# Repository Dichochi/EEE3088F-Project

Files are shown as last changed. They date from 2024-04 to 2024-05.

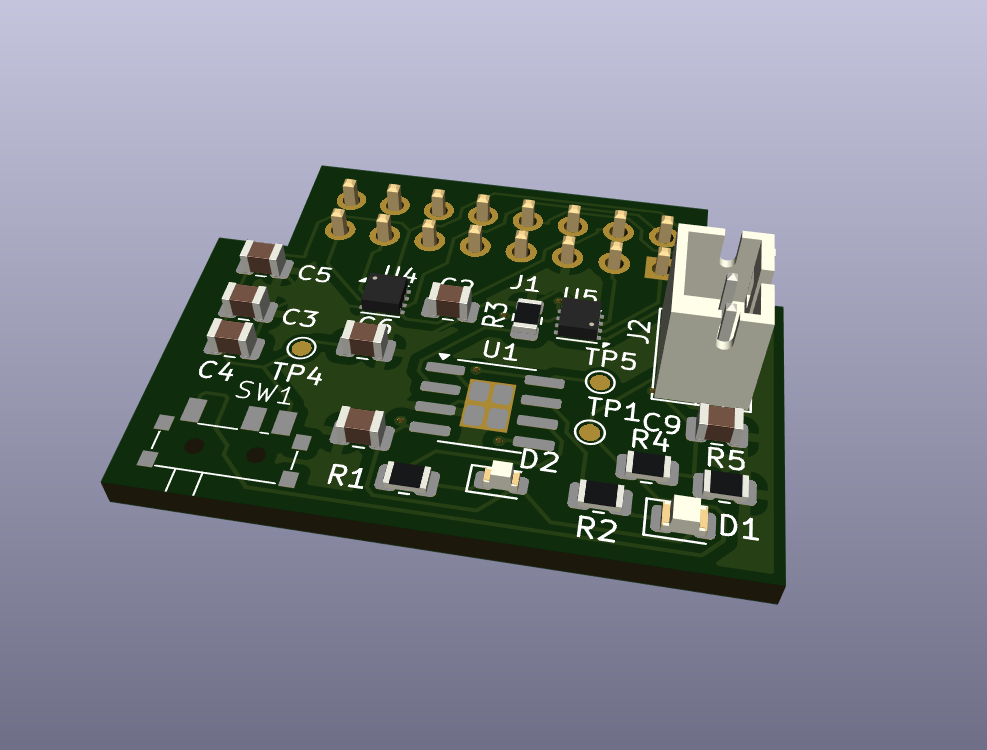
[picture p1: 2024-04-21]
Documents/Documents-Power/3D PCB.png

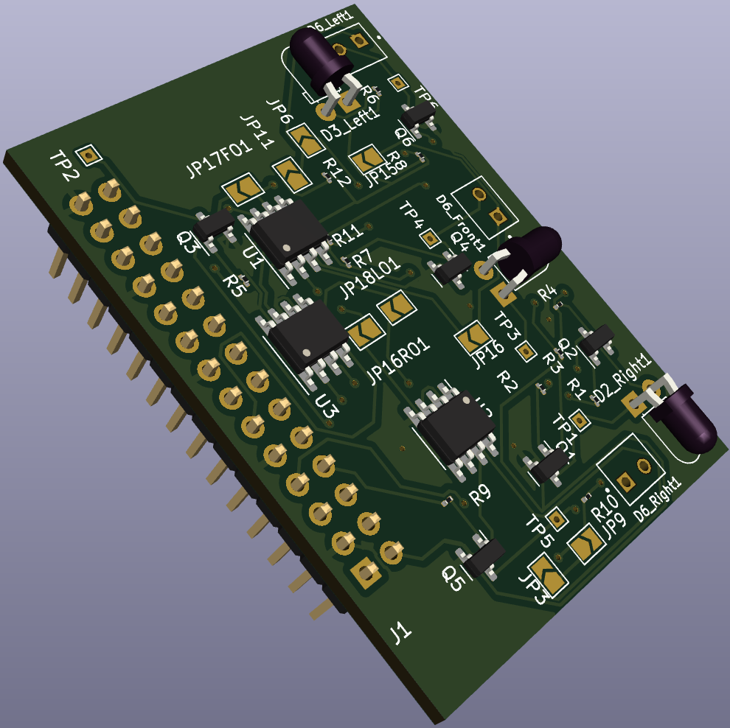
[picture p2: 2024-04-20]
Documents/Documents-Sensing/Sensor 3D view.png

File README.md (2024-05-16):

# EEE3088F-Project RMTDIC001 & NGMPHI006

## Description
This project is for the development and design of a Micro-Muse for EEE3088F 2024. The Micro Mouse contains a sesning Module, Power Module, as well as the main control unit(Mother-Board). The sensing system will sense obstacles in the proximity of the mouse, while the power module is mainly for powering the motors of the mouse and charging the on-board battery of the mouse. 

## Structure
* PCB: The KiCAD Project, Schematics & Layout and Project Libraries
* Firmware: Any software developed for the hardware or instructions on where to find relevant sofware
* Documents: Project documentation and component datasheets
* Production: The gerber files, BOM, Budget, or anything required by the fabrication houses
* Simulation: Any simulation files (eg SPICE) or design stage generated results (Eg matlab or excel) 

## Installation
--To be updated-- 

## Usage
The project documentation can be found in the [Documents](https://github.com/Dichochi/EEE3088F-Project/tree/main/Documents) directory and the files required to produce the PCB can be found in the [Production](https://github.com/Dichochi/EEE3088F-Project/tree/main/Production) directory.

## Contact
* Dichochi Ramotlou- RMTDIC001@myuct.ac.za
* Philasande Ngema - NGMPHI006@myuct.ac.za

## Project Status and Roadmap
This project is actively under developement.

## Authors and Acknowledgement
Authors:
* Dichochi Ramotlou
* Philasande Ngema

## License
[Creative Commons Attribution 4.0 International license](https://choosealicense.com/licenses/cc-by-4.0/)

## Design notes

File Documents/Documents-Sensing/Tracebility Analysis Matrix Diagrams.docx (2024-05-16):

R003:
The Sensor board should be the correct size for the Mouse.

AT002:
The freedom of movement of the Mouse should not be restricted by the sensor board., I.e. the Mouse is able to move around the maze.

SP003:
Using a board with dimensions not exceeding 40x70mm.

Verified by

Fulfilled by

AT003:
A significant change in the output when the obstacle is within an 80mm range, indicating that the ADC has captured the sense output.

R005:
The Mouse should be able to detect dead ends in the Maze.

SP002:
Three sets of sensing components a sensing range of 0-150mm, and angle spectrum of 0-60 °

Verified by

Fulfilled by

Why?

A maze dead end would be an obstacle in all three sense directions, if all the three sensing components are properly and equally calibrated, they should sense obstacles in their respective directions.

AT004:
Testing the switching behavior of the output.

SP001:
Utilizing PWM or input switching behavior so sensor turns on/off at a specific frequency and duty cycle of 50%.

R001:
Minimize Power Consumption.

Verified by

Fulfilled by

How?

The input square wave will have a duty cycle of 50%, for example if the Mouse remains on for 60s, the sensor will be off for 30s saving a lot of power.

AT001:
Observable change in output when obstacle is within 150mm of the mouse.

R004:
The Sensor board should be the able to communicate with the control unit using the correct communication protocol.

SP004:
Using I2C protocol on all ICs on the sensor board.

Verified by

Fulfilled by

Why?

To show that the sensor board works correctly an output should be observed if there is an obstacle in any of the sense directions.

AT001:
Observable change in output when obstacle is within 150mm of the mouse.

SP002:
Three sets of sensing components a sensing range of 0-150mm, and angle spectrum of 0-60 ° .

ROO2:
Valuable Sense Output from left right and forward directions.

Verified by

Fulfilled by

AT005:
The sensor should detect objects at oblique angles.

Fulfilled by

Verified by?

Although the sensing range is 150mm, what is eventually needed is a 0 or 1 to either light up an LED or turn it off when there is no obstacle, a close obstacle would be within 50mm of the Mouse.

Why?

Verified by

SP005:

Observable output voltage on ADC for all three sense directions.

AT003:
A significant change in the output when the obstacle is within an 80mm range, indicating that the ADC has captured the sense output.

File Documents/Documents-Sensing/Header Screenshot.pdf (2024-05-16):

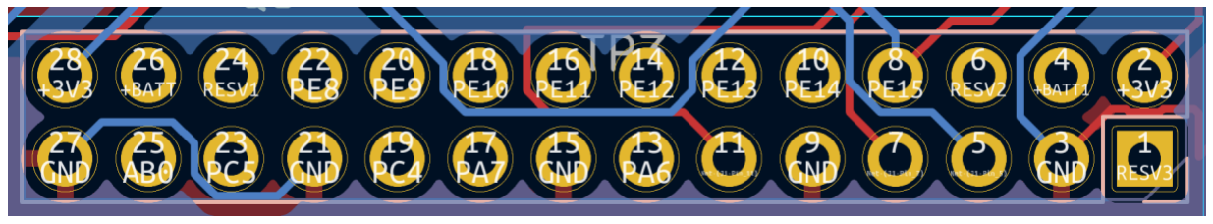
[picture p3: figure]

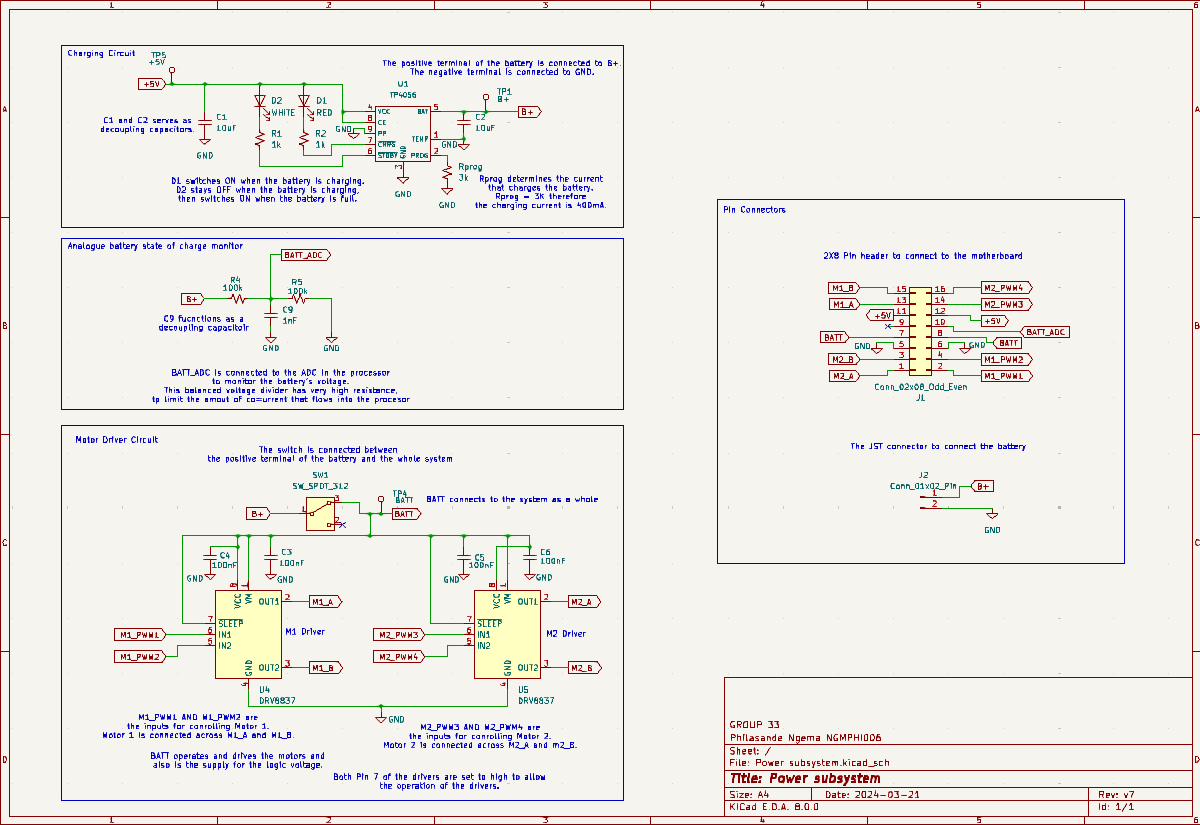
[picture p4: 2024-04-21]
Documents/Documents-Power/Final Schematic (1).png

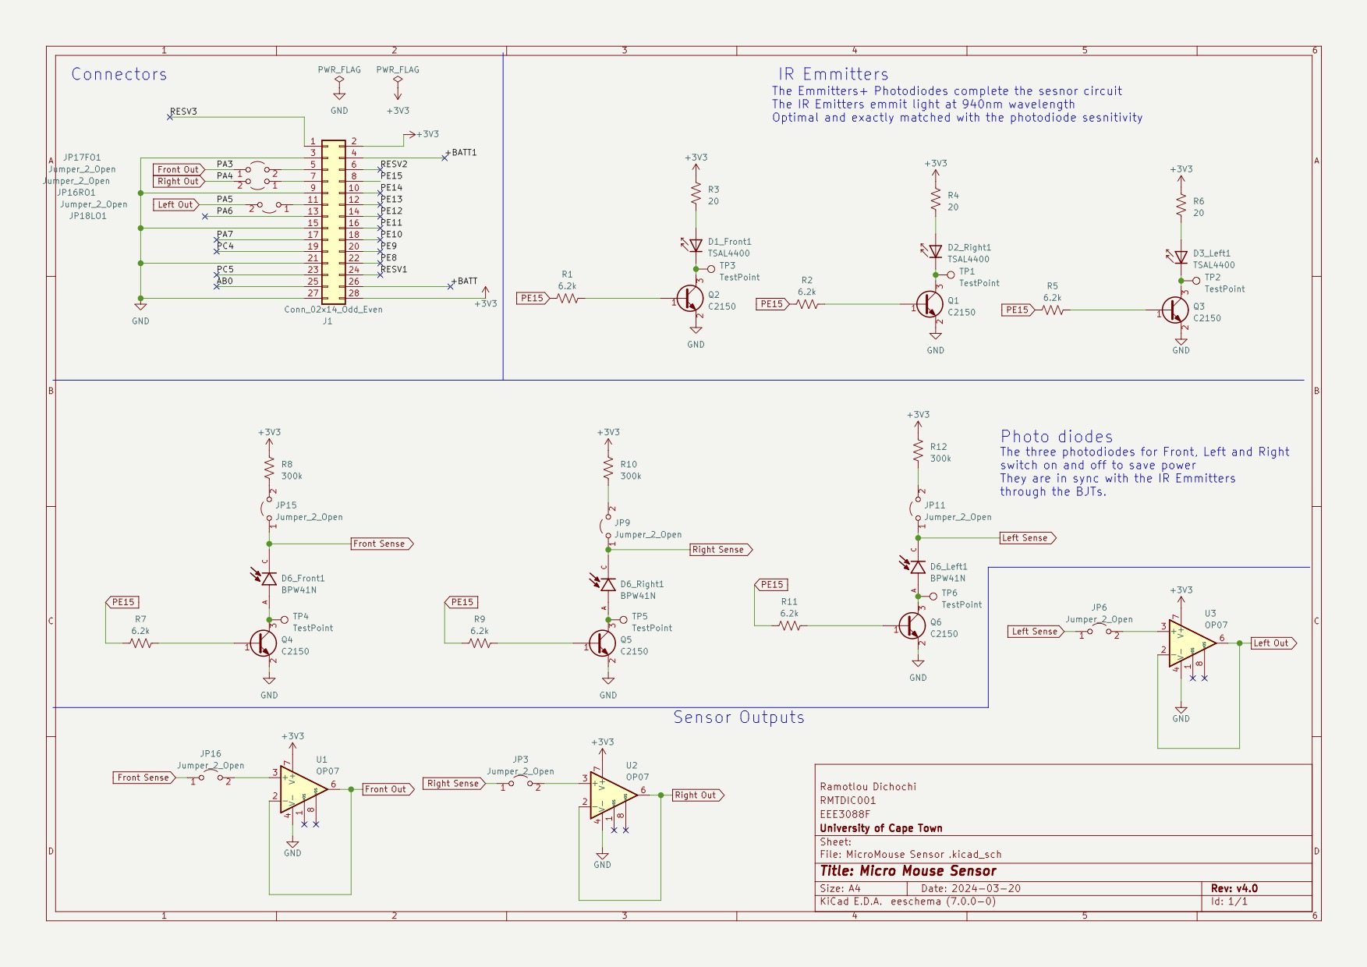
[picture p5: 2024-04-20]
Documents/Documents-Sensing/Sensor Mouse Schematic.jpg

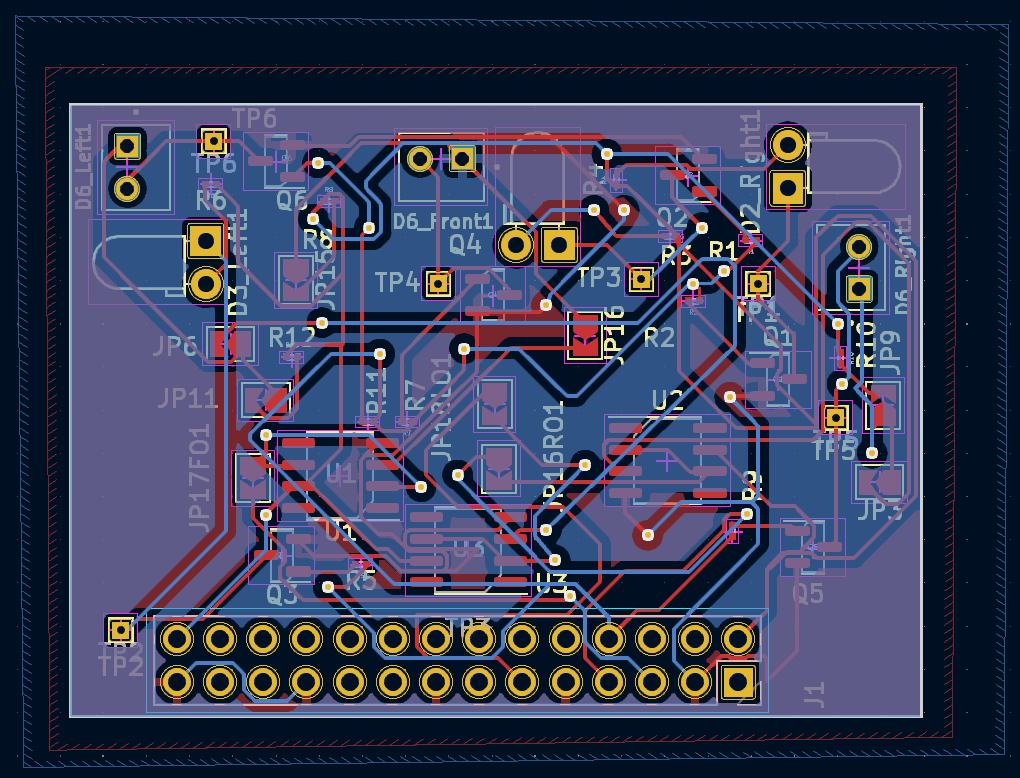
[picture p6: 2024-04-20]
Documents/Documents-Sensing/Sensor Back View .png

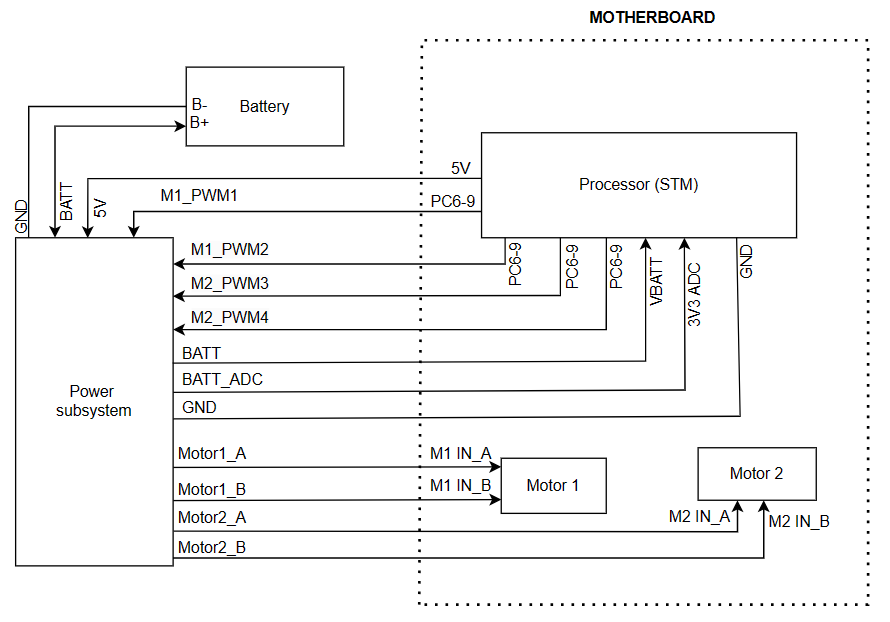
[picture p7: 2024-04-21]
Documents/Documents-Power/System Interfacing Diagram2.png

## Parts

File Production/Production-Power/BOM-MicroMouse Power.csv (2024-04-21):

Comment | Designator | Footprint | LCSC
100nF | C5 | C_0805_2012Metric
100nF | C4 | C_0805_2012Metric
100k | R4 | R_0805_2012Metric
DRV8837 | U5 | WSON-8-1EP_2x2mm_P0.5mm_EP0.9x1.6mm
RED | D1 | LED_0805_2012Metric
3k | R3 | R_0805_2012Metric
10uF | C2 | C_0805_2012Metric
100nF | C3 | C_0805_2012Metric
1nF | C9 | C_0805_2012Metric
1k | R1 | R_0805_2012Metric
DRV8837 | U4 | WSON-8-1EP_2x2mm_P0.5mm_EP0.9x1.6mm
1k | R2 | R_0805_2012Metric
10uF | C1 | C_0805_2012Metric
100k | R5 | R_0805_2012Metric
SW_SPDT_312 | SW1 | mySwitch
100nF | C6 | C_0805_2012Metric
TP4056 | U1 | SOIC-8-1EP_3.9x4.9mm_P1.27mm_EP2.29x3mm
WHITE | D2 | LED_0603_1608Metric

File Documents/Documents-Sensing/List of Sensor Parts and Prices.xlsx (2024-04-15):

Part | Mnaufacturer Code | JCLPCB Code | Quanity | Price | Extended Fee | Total
Op amp | OP07CDR | C7433 | 3 | 0.1593 | 0 | 0.4779
BJT | SS8050 | C2150 | 6 | 0.0139 | 0 | 0.0834
Photodiodes | BPW41N | C142586 | 3 | 0.489 | 1.5 | 2.967
IR Emmitter | TSAL4400 | C94135 | 3 | 0.1262 | 1.5 | 1.8786
6.2k Resistor | 0603WAF6201T5E | C4260 | 6 | 0.0009 | 0 | 0.0054
20 Resistor | 0603WAF200JT5E | C22950 | 3 | 0.0009 | 0 | 0.0027
300k Resistor | 0603WAF3003T5E | C23024 | 3 | 0.001 | 0 | 0.003
Total: | 5.418

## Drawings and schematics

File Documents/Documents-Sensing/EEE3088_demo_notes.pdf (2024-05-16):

## EEE3088F RMTDIC001 Demo Notes

FOR THE STM32

PA0-> LEFT ->LED7
PA1-> MIDDLE ->LED6
PA2-> RIGHT ->LED5

DON’T FORGET TO COMMON GROUND STM, SENSOR AND POWER SUPPLY

System Interface Input

Table 1: System Interface Table Sensor Board Input

Origin | Destination | Use
3V3 Supply | Pin 2(Sensor Board) | Power
GND Supply | Pin 3(Sensor Board) | Power
GND Supply | STM Ground Pin | Power
3V3 Supply | Pin 10(Sensor Board) | Input Power
3V3 Supply | Pin 22(Sensor Board) | Input Power
3V3 Supply | Pin 20(Sensor Board) | Input Power

System Interface Output

Table 2: System Interface Table Sensor Board Output

Origin | Destination | Use
Pin 5(Sensor Board) | PA1 STM | Front sense
Pin 7(Sensor Board) | PA2 STM | Right Sense
Pin 11(Sensor Board) | PA0 STM | Left Sense

1

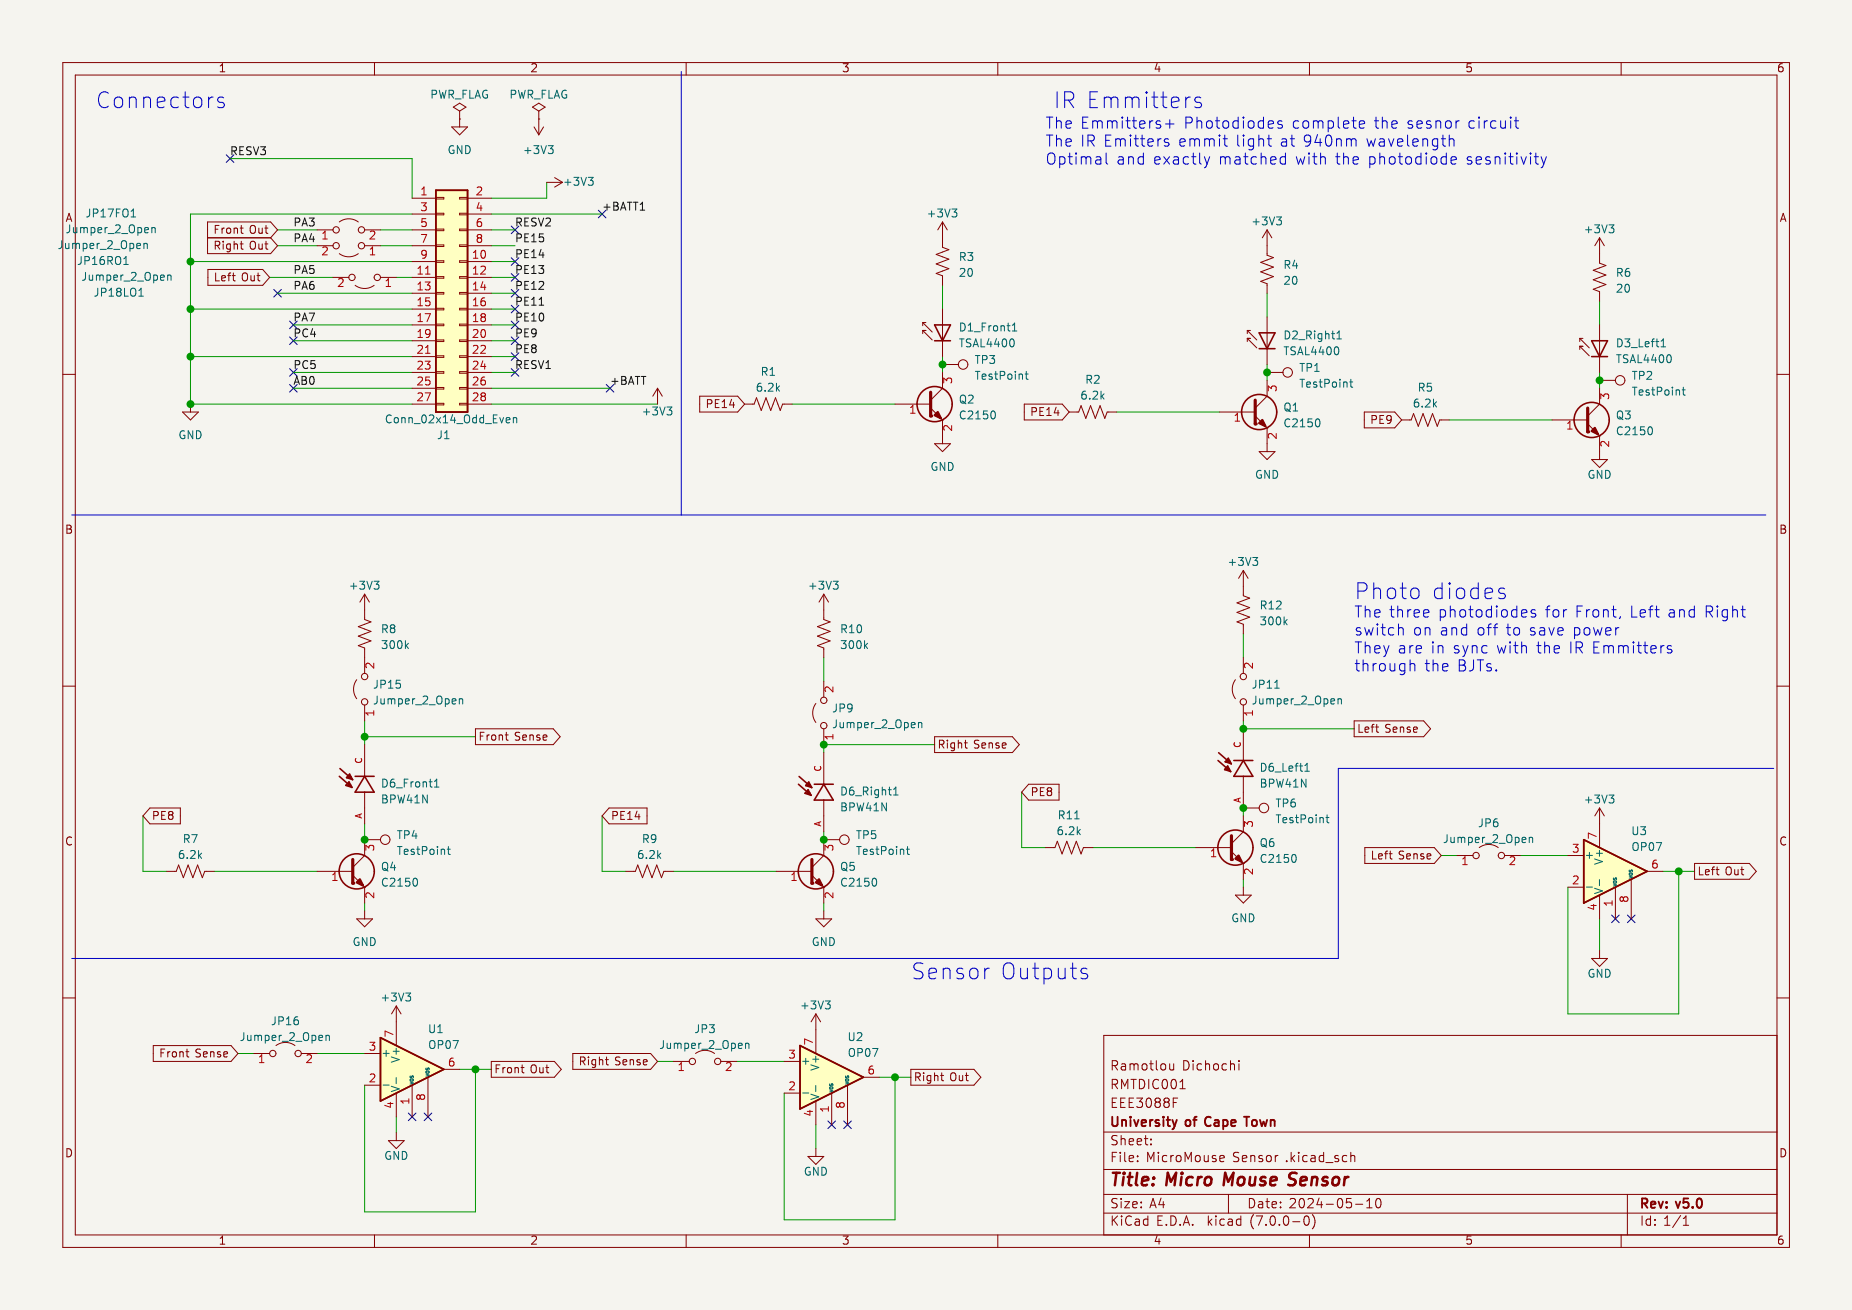
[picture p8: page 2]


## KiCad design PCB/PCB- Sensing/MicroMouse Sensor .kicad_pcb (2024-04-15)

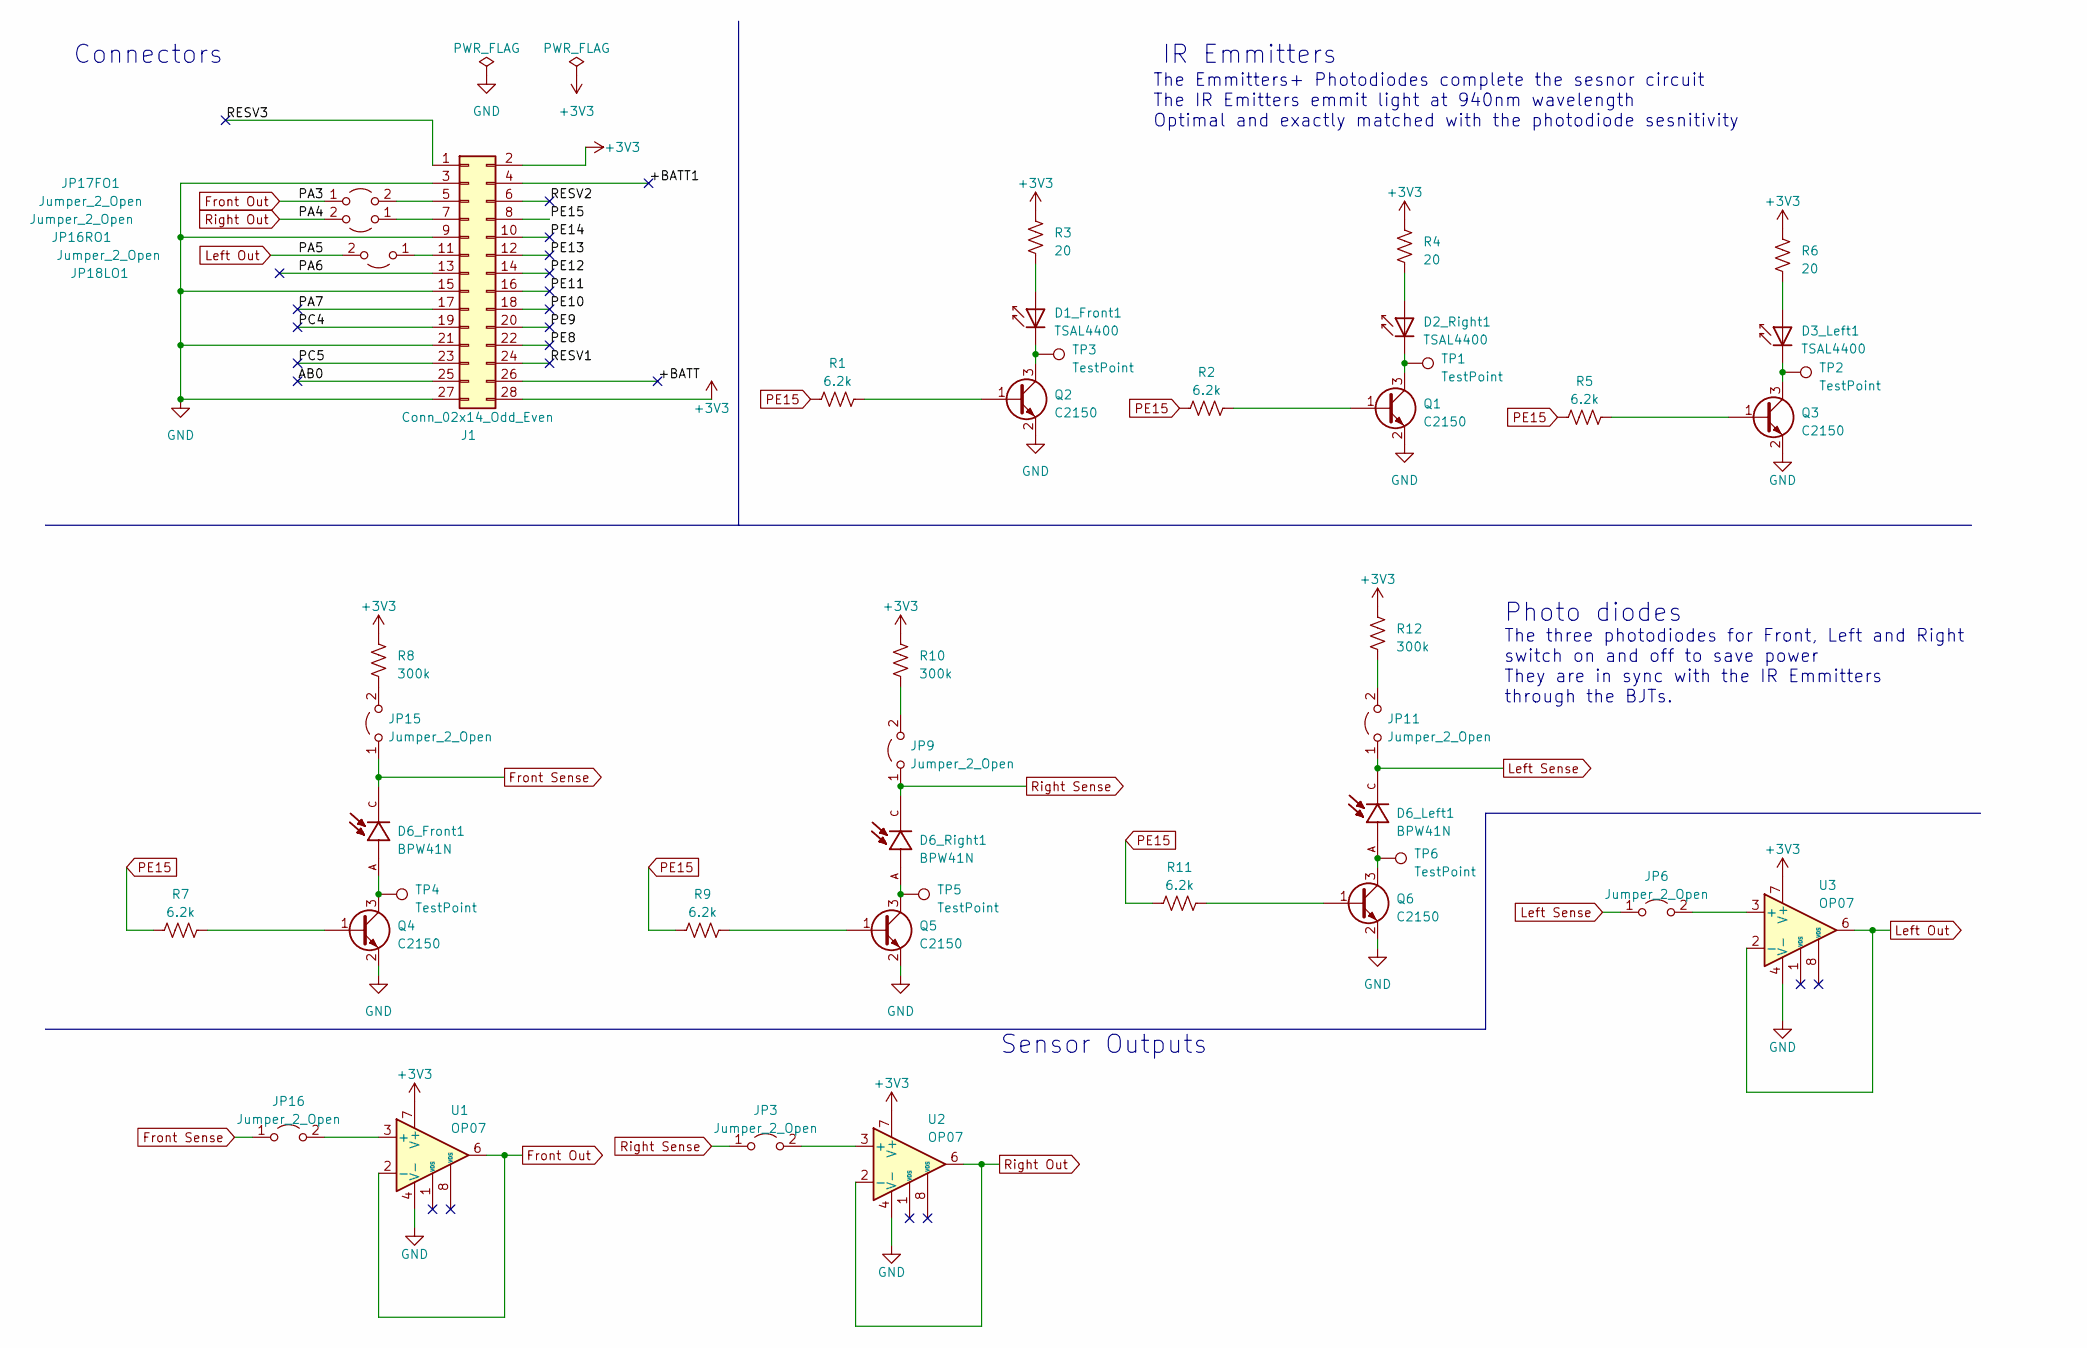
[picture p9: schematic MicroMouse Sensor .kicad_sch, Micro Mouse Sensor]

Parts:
D1_Front1, D2_Right1, D3_Left1: TSAL4400; LED_D3.0mm_Horizontal_O1.27mm_Z2.0mm_IRBlack
D6_Front1, D6_Left1, D6_Right1: BPW41N; DIO_BPW41N; PARTREV 1.6
J1: Conn_02x14_Odd_Even; PinHeader_2x14_P2.54mm_Vertical
JP3, JP6, JP9, JP11, JP15, JP16, JP16RO1, JP17FO1, JP18LO1: Jumper_2_Open; SolderJumper-2_P1.3mm_Open_TrianglePad1.0x1.5mm
Q1, Q2, Q3, Q4, Q5, Q6: C2150; SOT-23
R1, R2, R5, R7, R9, R11: 6.2k; R_0201_0603Metric
R3, R4, R6: 20; R_0201_0603Metric
R8, R10, R12: 300k; R_0201_0603Metric
TP1, TP2, TP3, TP4, TP5, TP6: TestPoint; TestPoint_THTPad_1.0x1.0mm_Drill0.5mm
U1, U2, U3: OP07; SOIC-8_3.9x4.9mm_P1.27mm

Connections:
+3V3: J1.2, J1.28, R3.1, R4.1, R6.1, R8.1, R10.1, R12.1, U1.7 (V+), U2.7 (V+), U3.7 (V+)
/+BATT: J1.26
/+BATT1: J1.4
/AB0: J1.25
/PA6: J1.13
/PA7: J1.17
/PC4: J1.19
/PC5: J1.23
/PE8: J1.22
/PE9: J1.20
/PE10: J1.18
/PE11: J1.16
/PE12: J1.14
/PE13: J1.12
/PE14: J1.10
/RESV1: J1.24
/RESV2: J1.6
/RESV3: J1.1
Front Out: JP17FO1.1 (A), U1.2 (-), U1.6
Front Sense: D6_Front1.C, JP15.1 (A), JP16.1 (A)
GND: J1.3, J1.9, J1.15, J1.21, J1.27, Q1.2 (E), Q2.2 (E), Q3.2 (E), Q4.2 (E), Q5.2 (E), Q6.2 (E), U1.4 (V-), U2.4 (V-), U3.4 (V-)
Left Out: JP18LO1.2 (B), U3.2 (-), U3.6
Left Sense: D6_Left1.C, JP6.1 (A), JP11.1 (A)
unnamed: D1_Front1.2 (A), R3.2
unnamed: D1_Front1.1 (K), Q2.3 (C), TP3.1
unnamed: D2_Right1.2 (A), R4.2
unnamed: D2_Right1.1 (K), Q1.3 (C), TP1.1
unnamed: D3_Left1.2 (A), R6.2
unnamed: D3_Left1.1 (K), Q3.3 (C), TP2.1
unnamed: J1.5, JP17FO1.2 (B)
unnamed: J1.7, JP16RO1.1 (A)
unnamed: J1.11, JP18LO1.1 (A)
unnamed: JP3.2 (B), U2.3 (+)
unnamed: JP6.2 (B), U3.3 (+)
unnamed: JP9.2 (B), R10.2
unnamed: JP11.2 (B), R12.2
unnamed: JP15.2 (B), R8.2
unnamed: JP16.2 (B), U1.3 (+)
unnamed: Q1.1 (B), R2.2
unnamed: Q2.1 (B), R1.2
unnamed: Q3.1 (B), R5.2
unnamed: Q4.1 (B), R7.2
unnamed: D6_Front1.A, Q4.3 (C), TP4.1
unnamed: Q5.1 (B), R9.2
unnamed: D6_Right1.A, Q5.3 (C), TP5.1
unnamed: Q6.1 (B), R11.2
unnamed: D6_Left1.A, Q6.3 (C), TP6.1
PE15: J1.8, R1.1, R2.1, R5.1, R7.1, R9.1, R11.1
Right Out: JP16RO1.2 (B), U2.2 (-), U2.6
Right Sense: D6_Right1.C, JP3.1 (A), JP9.1 (A)

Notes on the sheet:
Photo diodes
The Emmitters+ Photodiodes complete the sesnor circuit The IR Emitters emmit light at 940nm wavelength Optimal and exactly matched with the photodiode sesnitivity
Connectors
IR Emmitters
The three photodiodes for Front, Left and Right switch on and off to save power They are in sync with the IR Emmitters through the BJTs.
Sensor Outputs

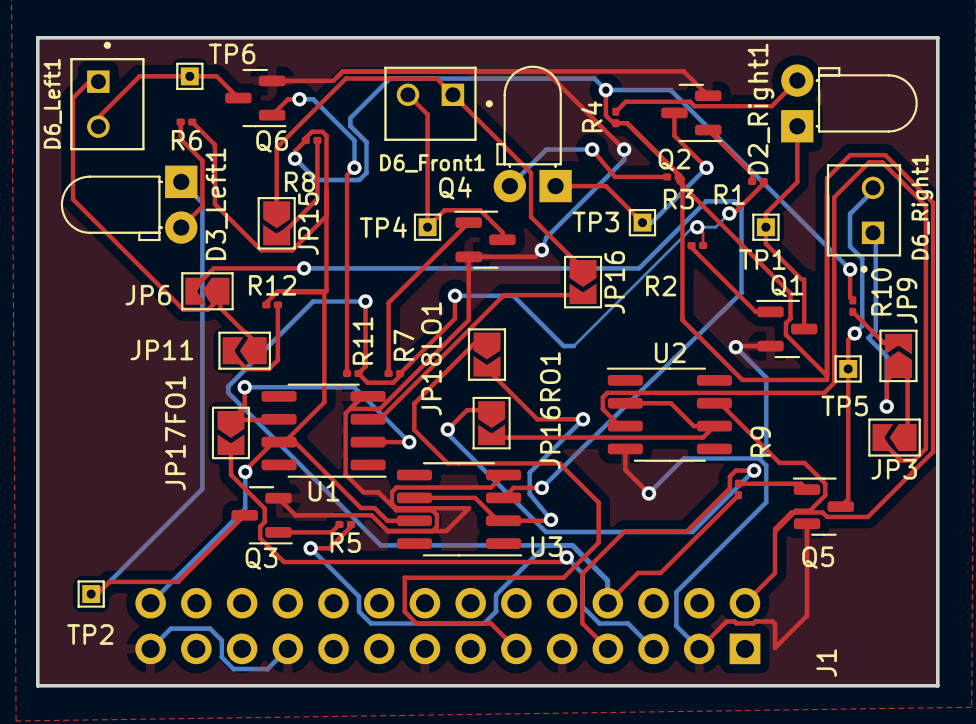
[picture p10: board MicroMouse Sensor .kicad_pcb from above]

Board: 2 copper layers, 50.0 x 36.0 mm, 43 parts (1 on the bottom side), 33 nets.

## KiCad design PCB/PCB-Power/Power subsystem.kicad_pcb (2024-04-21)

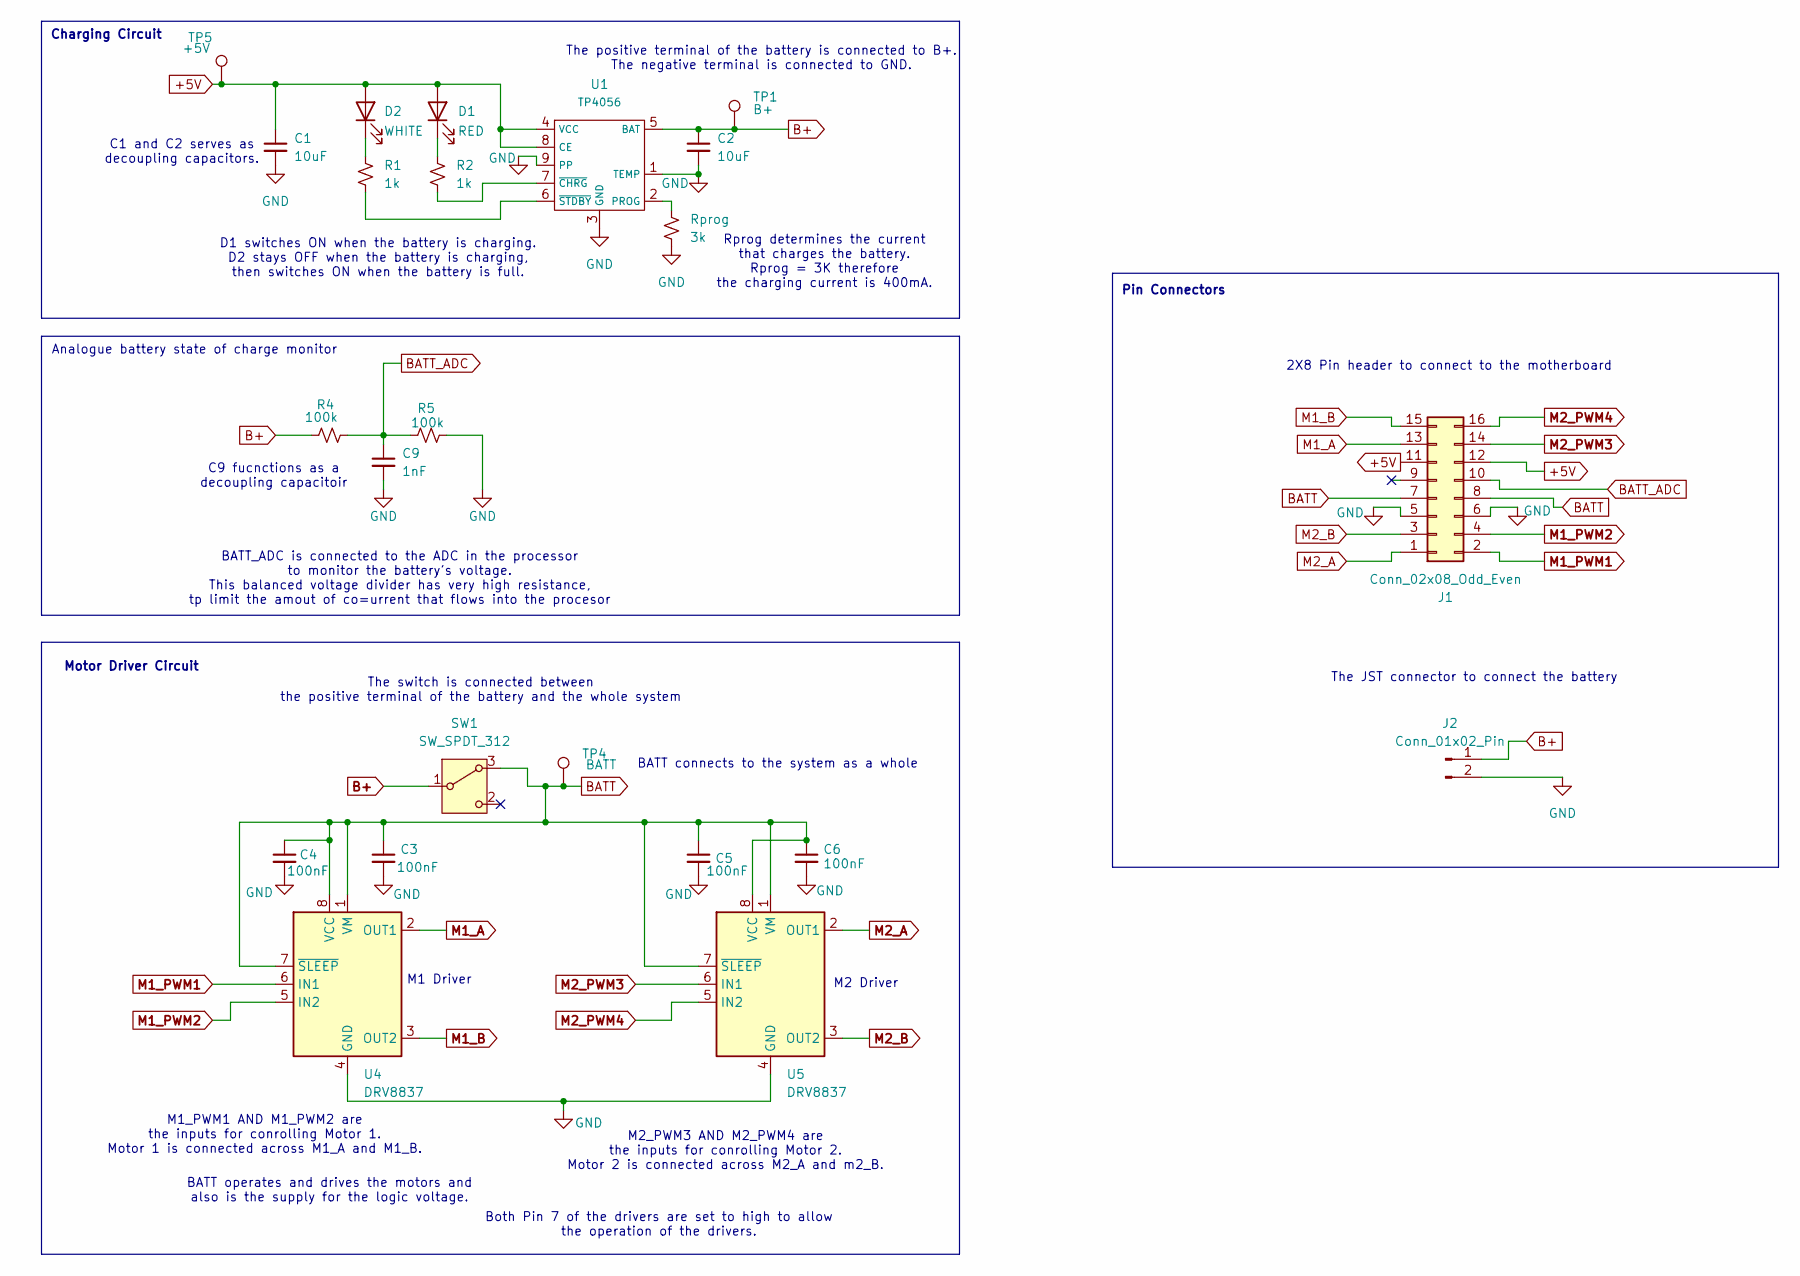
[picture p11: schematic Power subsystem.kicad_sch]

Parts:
C1, C2: 10uF; C_0805_2012Metric
C3, C4, C5, C6: 100nF; C_0805_2012Metric
C9: 1nF; C_0805_2012Metric
D1: RED; LED_0805_2012Metric
D2: WHITE; LED_0603_1608Metric
J1: Conn_02x08_Odd_Even; PinHeader_2x08_P2.54mm_Vertical
J2: Conn_01x02_Pin; JST_PH_B2B-PH-K_1x02_P2.00mm_Vertical
R1, R2: 1k; R_0805_2012Metric
R4, R5: 100k; R_0805_2012Metric
Rprog: 3k; R_0805_2012Metric
SW1: SW_SPDT_312; mySwitch
TP1: B+; TestPoint_Pad_D1.0mm
TP4: BATT; TestPoint_Pad_D1.0mm
TP5: +5V; TestPoint_Pad_D1.0mm
U1: TP4056; SOIC-8-1EP_3.9x4.9mm_P1.27mm_EP2.29x3mm
U4, U5: DRV8837; WSON-8-1EP_2x2mm_P0.5mm_EP0.9x1.6mm

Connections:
+5V: C1.1, D1.2 (A), D2.2 (A), J1.11, J1.12, TP5.1, U1.4 (VCC), U1.8 (CE)
B+: C2.1, J2.1, R4.1, SW1.1 (B), TP1.1, U1.5 (BAT)
BATT: C3.1, C4.1, C5.1, C6.1, J1.7, J1.8, SW1.3 (A), TP4.1, U4.1 (VM), U4.7 (~SLEEP), U4.8 (VCC), U5.1 (VM), U5.7 (~SLEEP), U5.8 (VCC)
BATT_ADC: C9.1, J1.10, R4.2, R5.1
GND: C1.2, C2.2, C3.2, C4.2, C5.2, C6.2, C9.2, J1.5, J1.6, J2.2, R5.2, Rprog.2, U1.1 (TEMP), U1.3 (GND), U1.9 (PP), U4.4 (GND), U4.9 (GND), U5.4 (GND), U5.9 (GND); also elsewhere on the board
M1_A: J1.13, U4.2 (OUT1)
M1_B: J1.15, U4.3 (OUT2)
M1_PWM1: J1.2, U4.6 (IN1)
M1_PWM2: J1.4, U4.5 (IN2)
M2_A: J1.1, U5.2 (OUT1)
M2_B: J1.3, U5.3 (OUT2)
M2_PWM3: J1.14, U5.6 (IN1)
M2_PWM4: J1.16, U5.5 (IN2)
unnamed: D1.1 (K), R2.1
unnamed: D2.1 (K), R1.1
unnamed 15: Rprog.1, U1.2 (PROG); also elsewhere on the board
unnamed: R2.2, U1.7 (~CHRG)
unnamed: R1.2, U1.6 (~STDBY)

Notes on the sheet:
M1 Driver
BATT connects to the system as a whole
The positive terminal of the battery is connected to B+. The negative terminal is connected to GND.
BATT operates and drives the motors and also is the supply for the logic voltage.
The JST connector to connect the battery
Both Pin 7 of the drivers are set to high to allow the operation of the drivers.
M2_PWM3 AND M2_PWM4 are the inputs for conrolling Motor 2. Motor 2 is connected across M2_A and m2_B.
Pin Connectors
Motor Driver Circuit
M1_PWM1 AND M1_PWM2 are the inputs for conrolling Motor 1. Motor 1 is connected across M1_A and M1_B.
M2 Driver
The switch is connected between the positive terminal of the battery and the whole system
2X8 Pin header to connect to the motherboard
Rprog determines the current that charges the battery. Rprog = 3K therefore the charging current is 400mA.
C1 and C2 serves as decoupling capacitors.
C9 fucnctions as a decoupling capacitoir
Analogue battery state of charge monitor
D1 switches ON when the battery is charging. D2 stays OFF when the battery is charging, then switches ON when the battery is full.
BATT_ADC is connected to the ADC in the processor to monitor the battery's voltage. This balanced voltage divider has very high resistance, tp limit the amout of co=urrent that flows into the procesor
Charging Circuit

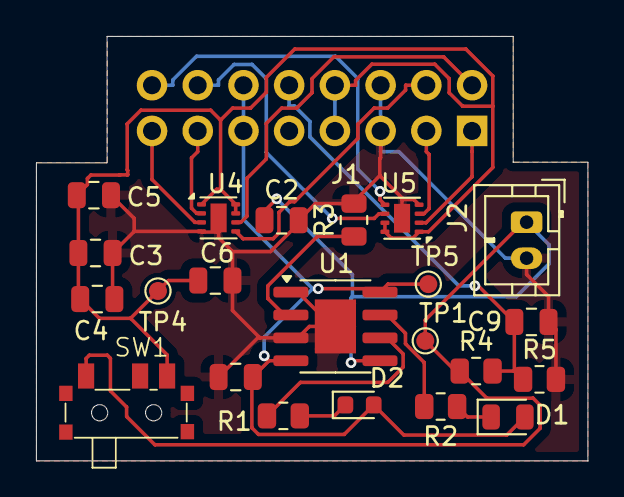
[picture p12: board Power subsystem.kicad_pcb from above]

Board: 2 copper layers, 30.6 x 23.6 mm, 23 parts (1 on the bottom side), 18 nets.

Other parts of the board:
R3: 3k; R_0805_2012Metric

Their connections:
GND: R3.2; also elsewhere on the board
unnamed 15: R3.1; also elsewhere on the board

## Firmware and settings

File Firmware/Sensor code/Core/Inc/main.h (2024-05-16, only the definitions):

#define LED0_Pin GPIO_PIN_0
#define LED0_GPIO_Port GPIOB
#define LED5_Pin GPIO_PIN_5
#define LED5_GPIO_Port GPIOB
#define LED6_Pin GPIO_PIN_6
#define LED6_GPIO_Port GPIOB
#define LED7_Pin GPIO_PIN_7
#define LED7_GPIO_Port GPIOB

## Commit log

2024-04-15 Sensor Gerber Files
    [BOM-MicroMouse Sensor .csv, List of Parts and Prices.xlsx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]
2024-04-15 Clearing up Folders
    [BOM-MicroMouse Sensor .csv, List of Parts and Prices.xlsx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]
2024-04-16 File Modifications
    [List of Sensor Parts and Prices.xlsx]
2024-04-20 Sensor documents
2024-04-21 Sensor Document
2024-04-21 Power document
    [BOM-MicroMouse Power.csv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]
2024-04-21 Sorting out files
    [BOM-MicroMouse Power.csv, BOM-MicroMouse Sensor .csv, List of Sensor Parts and Prices.xlsx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]
2024-05-16 Sensor Documents Update
    [MicroMouse Sensor .kicad_sch]
2024-05-16 Sensor code upload

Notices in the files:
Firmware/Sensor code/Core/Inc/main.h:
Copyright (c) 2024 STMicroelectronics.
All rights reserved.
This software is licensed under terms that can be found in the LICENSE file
